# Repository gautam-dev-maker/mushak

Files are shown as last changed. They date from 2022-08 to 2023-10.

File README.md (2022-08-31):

<p align="center">
  
</p>

# About The Project

Mushak is a micromouse maze solving bot. The aim of this project is to make India's first and smallest half-size micromouse bot. "Mushak" in hindi means "Mouse".

This micromouse consist of a very small coreless motors (6 mm width and 10 mm length) and PCB as it's base . Since coreless motors doesn't provide enough torque for the movements of bot we used gear box to increase the torque.

Mushak is of size 45.7mm x 40.0 mm, which is smaller than similar micromouse using STM32F405RG. We boast of least area consuming micromouse made using STM32 LQFP64 package chips.

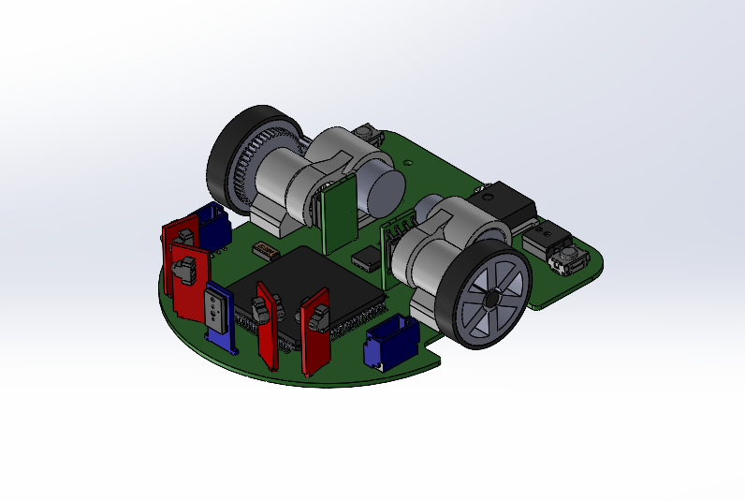
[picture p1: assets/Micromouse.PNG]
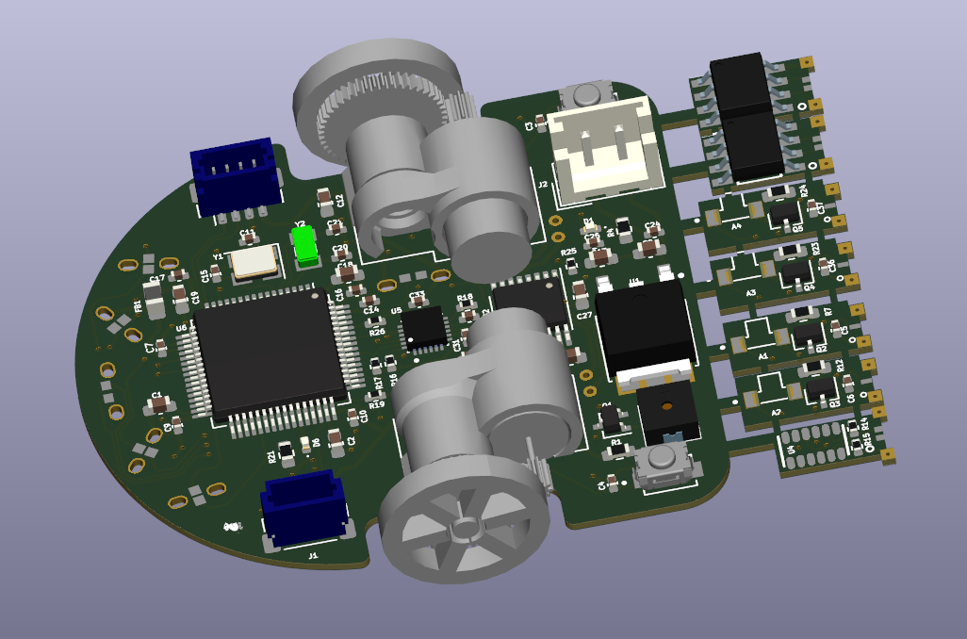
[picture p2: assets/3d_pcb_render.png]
|             |  |
:-------------------------:|:-------------------------:

# Table of Content
- [About The Project](#about-the-project)
- [Table of Content](#table-of-content)
- [File Structure](#file-structure)
- [PCB Design](#pcb-design)
    - [Major components used in the PCB include -](#major-components-used-in-the-pcb-include--)
  - [IR sensors](#ir-sensors)
    - [Placement of IR Sensors](#placement-of-ir-sensors)
  - [Power Distribution](#power-distribution)
  - [STM32F405RG (Microcontroller)](#stm32f405rg-microcontroller)
  - [DRV8833 (Motor Driver)](#drv8833-motor-driver)
  - [VL6180X (ToF Sensor)](#vl6180x-tof-sensor)
  - [HC-08 (BLE Module)](#hc-08-ble-module)
  - [AS5600 (Magnetic Encoder)](#as5600-magnetic-encoder)
  - [MPU6500 (IMU)](#mpu6500-imu)
  - [Routing](#routing)
  - [Solutions to some of the major problems faced while designing PCB](#solutions-to-some-of-the-major-problems-faced-while-designing-pcb)
- [CAD Design](#cad-design)
  - [Part Descriptions](#part-descriptions)
  - [Issues Faced in Mechanical Designing](#issues-faced-in-mechanical-designing)
    - [Designing Mount](#designing-mount)
    - [Finalising and Meshing the gears](#finalising-and-meshing-the-gears)
- [Firmware](#firmware)
  - [File Structure](#file-structure-1)
  - [Pinout of STM32F405RG](#pinout-of-stm32f405rg)
    - [Communication Buses](#communication-buses)
    - [ADC](#adc)
    - [PWM](#pwm)
    - [GPIO](#gpio)
  - [How To Use The Firmware](#how-to-use-the-firmware)
    - [Install gcc-arm-none-eabi compiler tool suite](#install-gcc-arm-none-eabi-compiler-tool-suite)
    - [Install ST-Link Toolchain](#install-st-link-toolchain)
    - [Build the source code](#build-the-source-code)
    - [Flash on the STM32 device](#flash-on-the-stm32-device)
- [Resources](#resources)
- [Acknowledgements](#acknowledgements)
- [License](#license)

# File Structure

    .
    ├── Assets             # Documentation files screenshots, gifs, videos of results
    ├── firmware           # contains required code for controlling the bot
    ├── pcb_design         # PCB files made in  kicad 6
    ├── cad_design         # CAD files of mushak (micromouse)
    ├── LICENSE            # License for this project
    └── README.md          # Contains documentation and information about this project

Further file structure of each folder is given in below sections.

# PCB Design

The Mushak PCB design is made on the latest version of KiCAD 6.

Mushak is designed over STM32F405RG microcontroller accomodated with various sensors and drivers for the micromouse.

We designed the smallest micromouse that is based on STM32F405RG microcontroller

<p align="center">
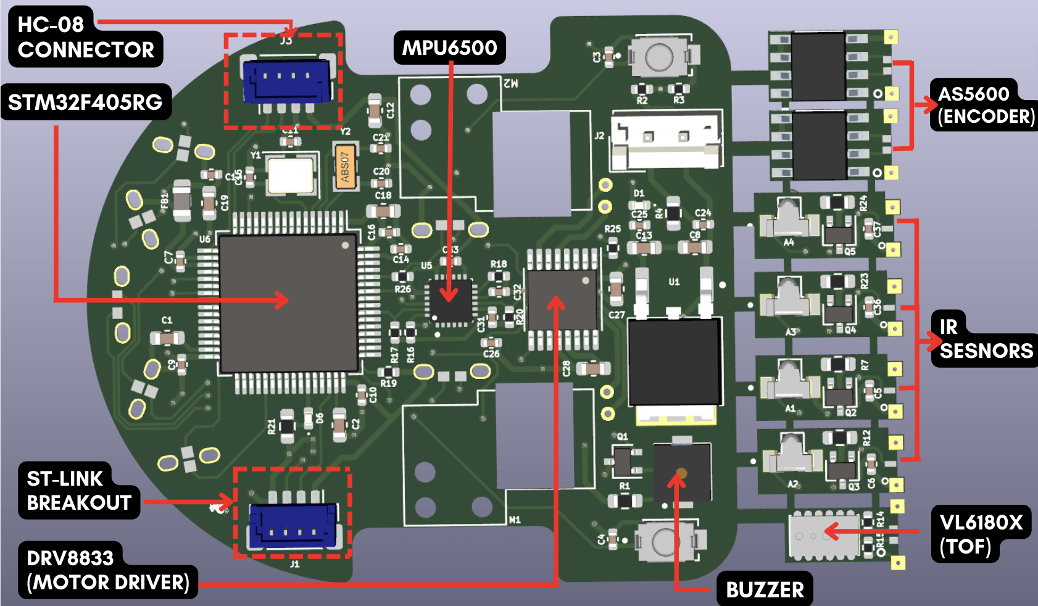
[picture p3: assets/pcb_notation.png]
  
</p>

### Major components used in the PCB include -

| Components | Description |
| --- | --- |
| STM32F405RG | Microcontroller |
| VL6180x | ToF sensor4 |
| DRV8833 | Motor Driver |
| MPU6500 | IMU |
| SFH-4045N | Infrared Emitter |
| SFH-3015-FA | Phototransistor (Reciever) |

---

## IR sensors

* The IR sensors include majorly two components, IR emitter which emits the Infrared light of a particular wavelength which is not visible with the human eye. 

* This light gets reflected back from the obstacle present in form of the robot to the photo transistor, when the Infrared light of this perticular wavelength enters the phototransistor device it allows the current to flow from the collector to the emmiter of device. This current flow creates a voltage drop across the resistor connected with the photo transistor and this voltage drop is read by th ADC of the microcontroller which varies as the intensity of light reflected changes. By this way we can determine how far is the obstacle from the robot.

* For controlling the intensity of the transmitted light we used N-Channel Mosfet whose gate is controlled by PWM signal given by the microcontroller.
By varying the PWM duty cycle we can control the intensity of the transmitted light from IR emmiter by which we can control the distance sensitivity.

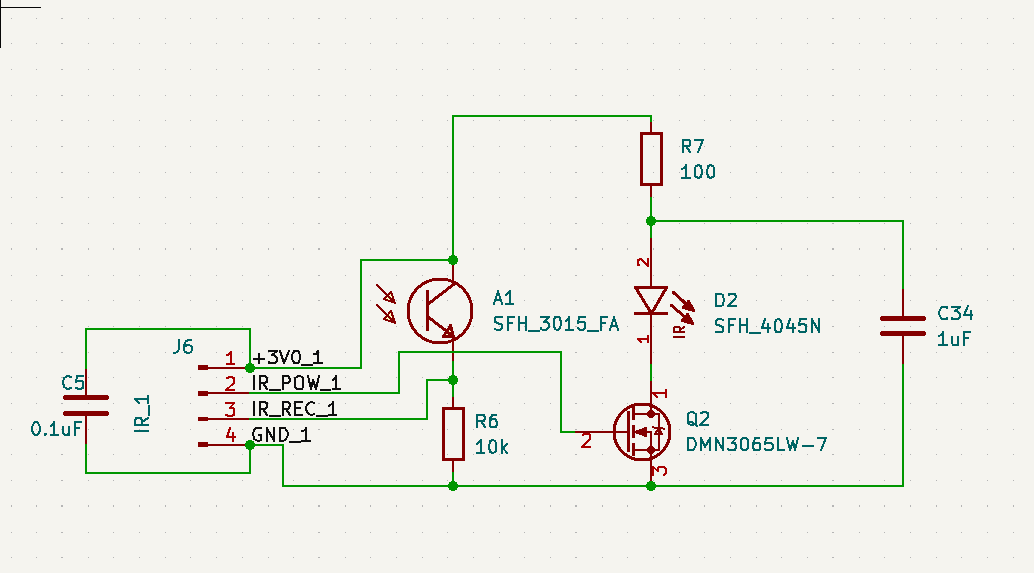
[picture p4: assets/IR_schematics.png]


* Four Sensor pairs are being used in Mushak (Micromouse)

### Placement of IR Sensors

Placing IR sensors pose a challenge, and required rigorous testing and brain storming. 

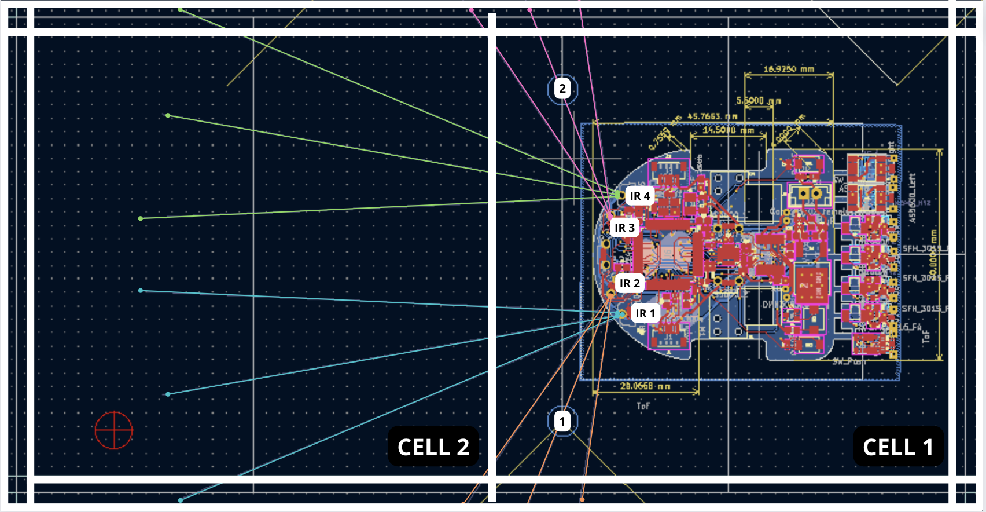
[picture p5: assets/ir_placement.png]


As can be seen in the image above we have visualised 2 cell based maze and bot is placed in first cell.

* `IR1` (blue rays) is pointing to the left mid point of next cell.
* `IR2` (orange rays) is pointing to the left end of current cell.
* `IR3` (pink rays) is pointing to the right end of current cell.
* `IR4` (green rays) is pointing to the right end of current cell.

To move the bot in straight line along the diagonal maze pattern , we have considered `point 1` and `point 2`. These two points are the edges of diagonal ends of above pattern . So if bot had to move diagonally we can check for readings at these two points and control the bot accordingly.

---

## Power Distribution
* Power to the control circuits is provided by 3V linear Regulator(LDO) which can provide upto 1A current. Power to the motor is directly given to the motor driver through battery.
* Additional capacitors are added across outputs for filtering out the voltage. Voltage divider resistors are being used to monitor the battery voltage. Power indication LED has been provided in the PCB. The input voltage for the PCB is 3.7 voltage through a general LiPo battery.

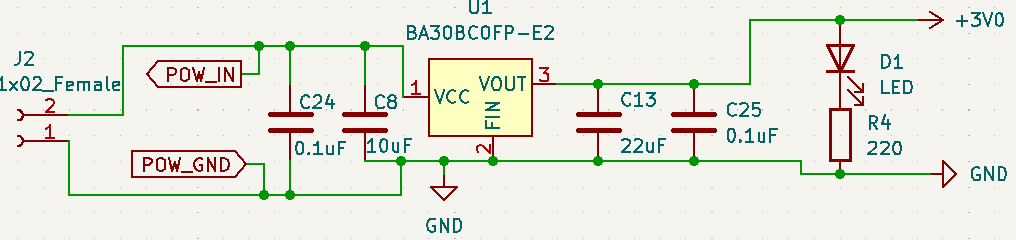
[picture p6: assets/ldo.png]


--- 

## STM32F405RG (Microcontroller)

The below image shows the pinout of STM32F405RG that we will be using for this project :

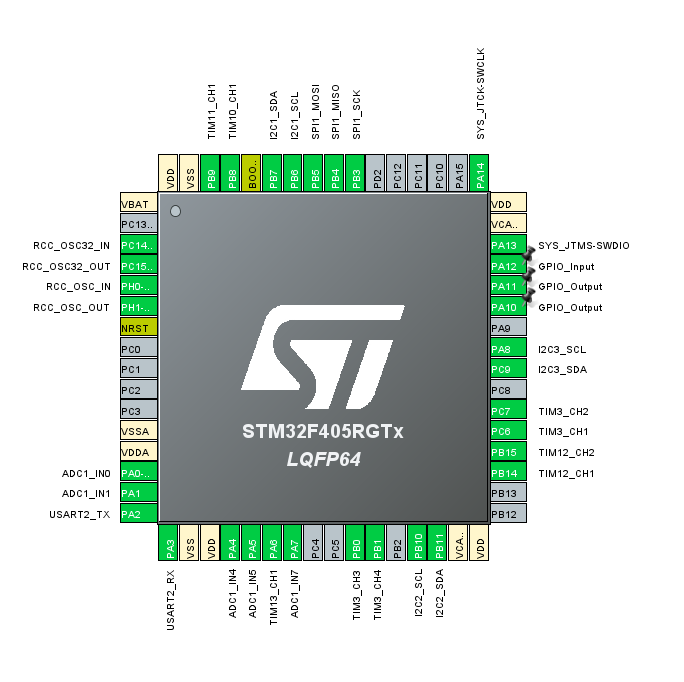
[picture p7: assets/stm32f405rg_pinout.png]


Decoupling capacitors of 0.1uF are connected near the vdd pins of STM32. Additional external low and high frequency oscillators are added for precise timing.

- HSE(High Speed External) clock - 25 Mhz
- LSE(Low Speed External) clock - 32.769 Khz

Filter circuit is being used for filtering out the analog reference voltage. Additional Debug switches are being added for debugging purposes

---
## DRV8833 (Motor Driver)

* We have used H-bridge motor driver which can control two motors at the same time via PWM (pulse width modulation) from the STM32F405RG (microcontroller).

* The motor driver can supply 1.5 Amps of current per motor which is enough to power up the coreless motors. 

* This motor driver keeps the controls terminals from the microcontrolller isolated from noise and high volatages of the motor power supply.

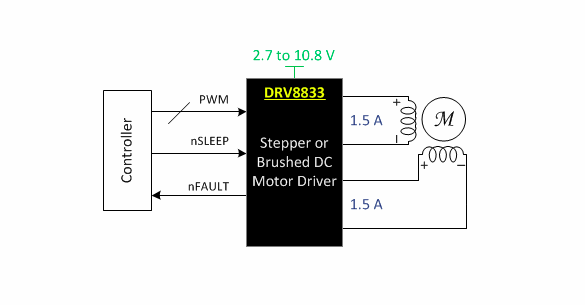
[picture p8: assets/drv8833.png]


---

## VL6180X (ToF Sensor)

* We added a Time of Flight sensor in front of the robot to measure the distance of the obstacle in front from the robot.

* This sensor measures the time taken by the light signal to get reflected from the obstacle and then measures the distace of the obstacle from the robot.

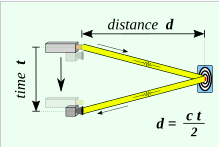
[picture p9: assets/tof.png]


* The sensor uses I2C protocol for communication with the microcontroller and send the distance values. It also has an additional feature of sensing the ambeint light which we can use to avoid the problems faced with IR sensors due to varing ambient light conditions.
* Due to cost issues it is not feasible to replace IR sensors with VL6180x, else it could have been a replacement.

---

## HC-08 (BLE Module)

* We used a BLE(Bluetooth Low Energy) module to communicate to the robot. It is one of the most important modules that is being used in mushak, this bluetooth module will enable us to communicate with the robot and precisely tune it to solve the mazes, additionally it makes debugging easier for us making Mushak user friendly.

* The module consumes very less power(since it works on BLE) and works on UART communication to talk with the microcontroller.

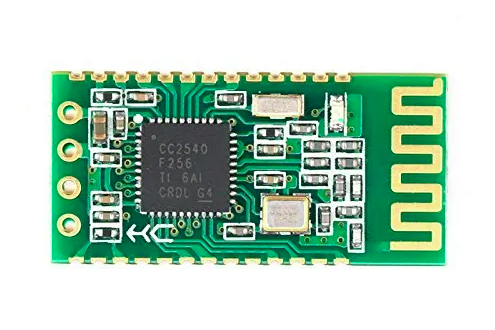
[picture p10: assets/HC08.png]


* For attaching this module we have provided the JST connectors to connect this module externally when required.

---

## AS5600 (Magnetic Encoder)

* To measure the RPM and the distance that the robot has covered we needed a type of encoder feedback. For this we used AS5600 magnetic encoders to measure the amount of rotation of the robot wheel.

* The magnetic encoders are mounted in an innovative way due to which no external mounts were required for their placement. Since magnets need to be right infront of the IC of AS5600 to get proper reading, we have taken extra care with mount size and shaft placement.

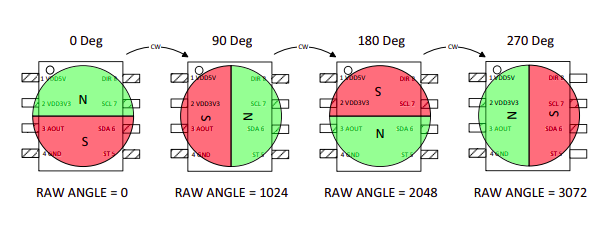
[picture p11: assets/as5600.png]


* The sensor works on I2C communication protocol to provide the reading to the microcontroller.

---

## MPU6500 (IMU)

* This sensor gives the feedback of orientaion of the robot. This MEMS based chip has in-built Acclereometer and Gyroscope by which it can determine its orietation with respect to space.

* This sensor works on SPI as well as I2C communication protocol but in our case to get the fastest data transfer, we used use SPI communcation.

---

## Routing

* Front Copper Layer:

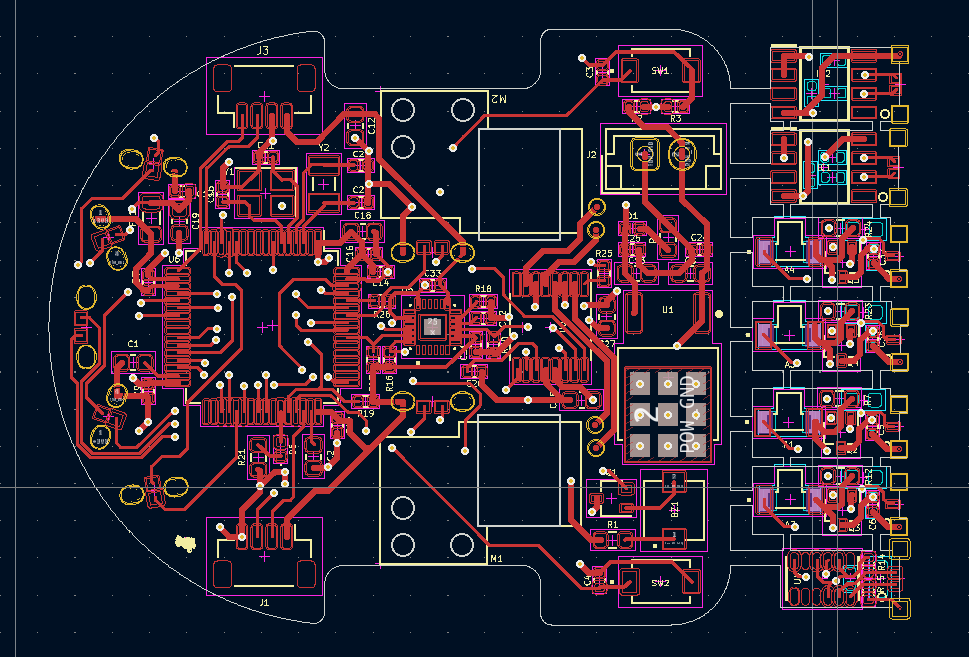
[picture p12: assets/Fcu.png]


* Back Copper Layer:

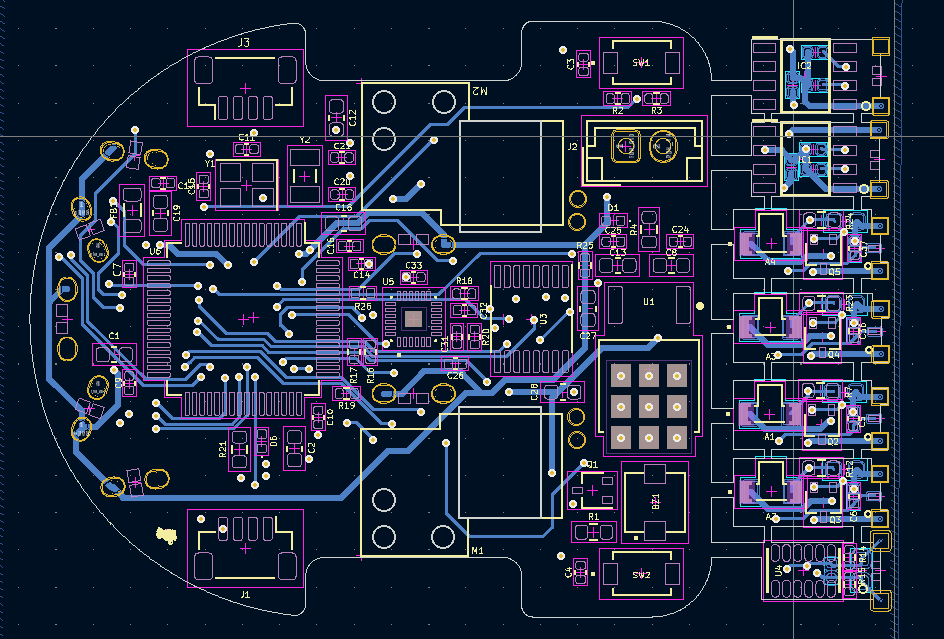
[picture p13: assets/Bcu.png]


* Final Routing:

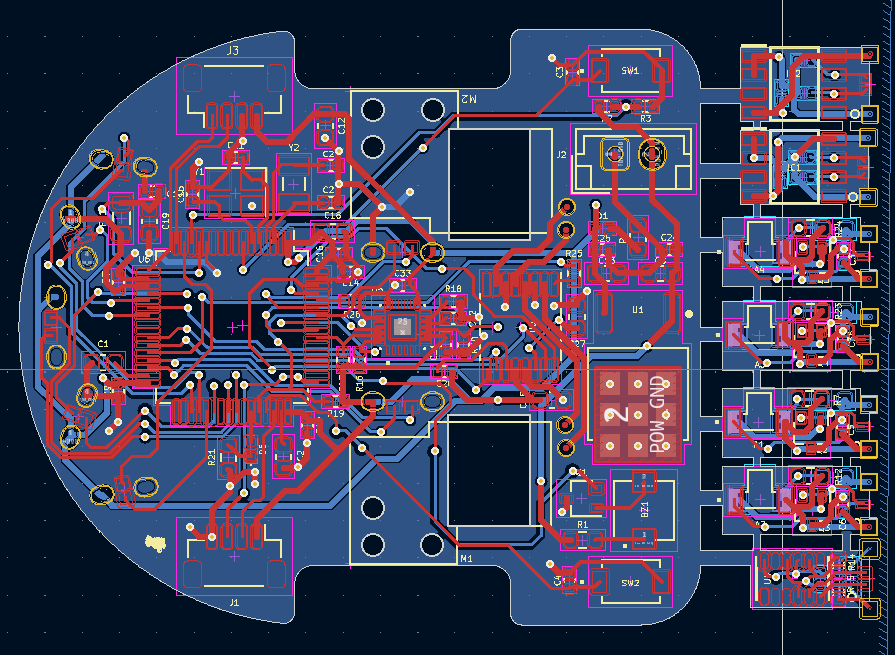
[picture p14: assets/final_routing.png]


For routing of the control circuitry we used traces of 0.2mm width and for power connections we used 0.4mm width tracks to ensure fairly high current flow.

## Solutions to some of the major problems faced while designing PCB

1) Minimalising passive components is a really hard task. So to solve this I properly reffered the application notes and datasheet of stm32f405RG. Moreover the design is well tested on simulation platform.

2) Efficient placement of components to reduce the size of the PCB. Innovative design to fix sensors and encoders in such a small space.

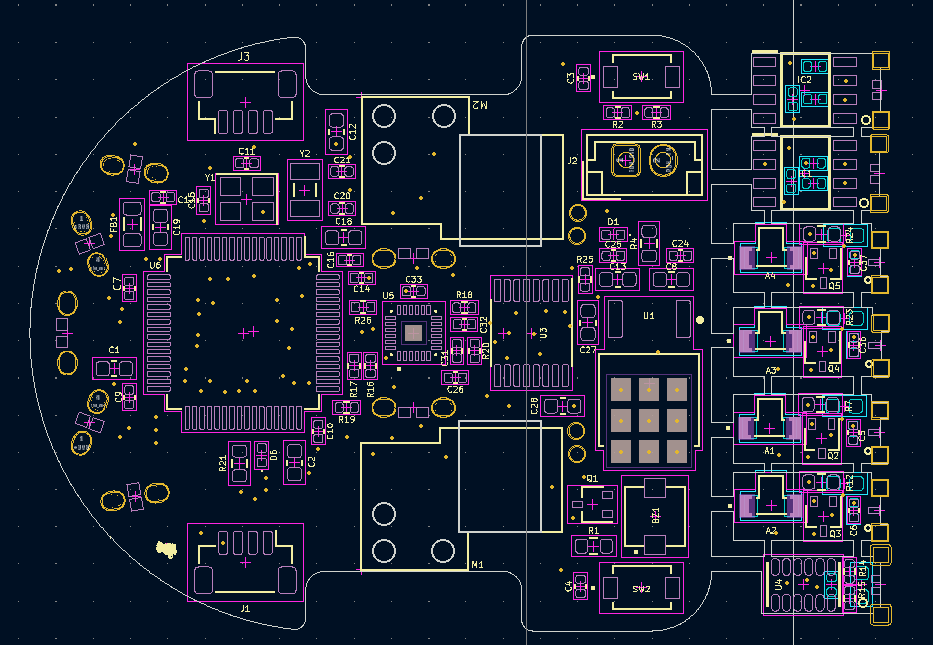
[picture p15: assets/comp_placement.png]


3) Since IRs are sensitive to ambient light we required a mechanism to adjust the brighness of IR Emitter. So to do that we used a mosfet based circuit, so brightness can be controlled using PWM.

4) It was a big challenge to place 90+ SMD and THT components on a small size PCB of just 45.7x40mm size.

# CAD Design

CAD design consist of 3D modeling of Bot design.Before design can be made on PCB, we need to check if various other aspects of systems and mechanical design satisfy our requiements. So CAD design form a very important part of our project.

## Part Descriptions
* The bot contains a total of 6 main **mechanical** components which are as listed in the following table :

| Parts | Description |
| --- | --- |
| <p align="center">
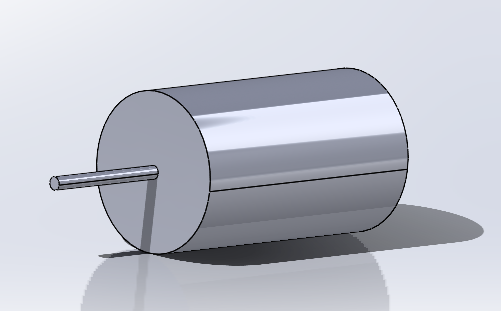
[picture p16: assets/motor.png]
   | Motors - This motor has </br> dimensions: Length x Dia. 12 x 6 mm and a shaft lenght of 6mm.|
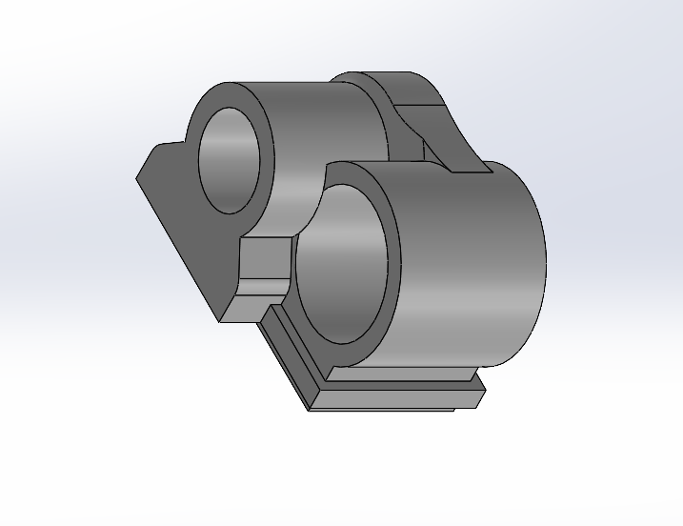
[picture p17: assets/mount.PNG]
   | Motor_mount - This is the mount for the motors, which holds </br> the motor, shaft, gears, bearing and magnet.Because of less center-to-center distance between gears, after many iterations this mount was designed.|
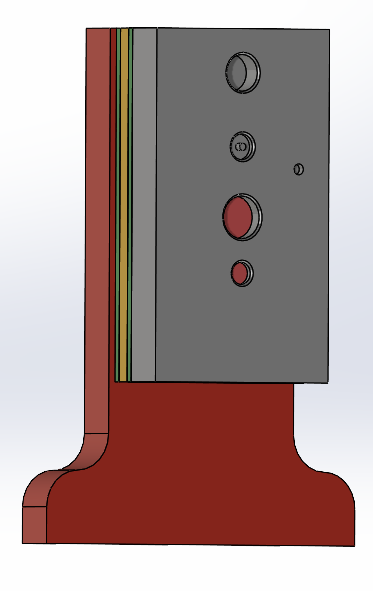
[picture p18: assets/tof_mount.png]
   | TOF_mount - This is the mount for TOF sensor, which is placed </br> in front. We have used VL6180x TOF sensor.|  
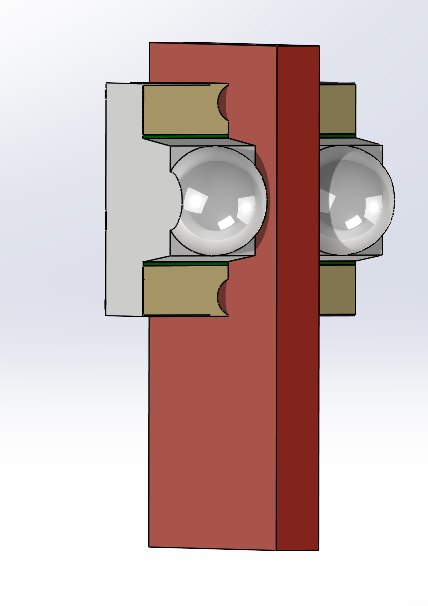
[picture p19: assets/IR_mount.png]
    | IR_mounts - These are the mounts for IR sensors placed </br> at specific angles. SFH-3015-FA and SFH-4045N sensors are phototransistors and IR emitters respectively.|   
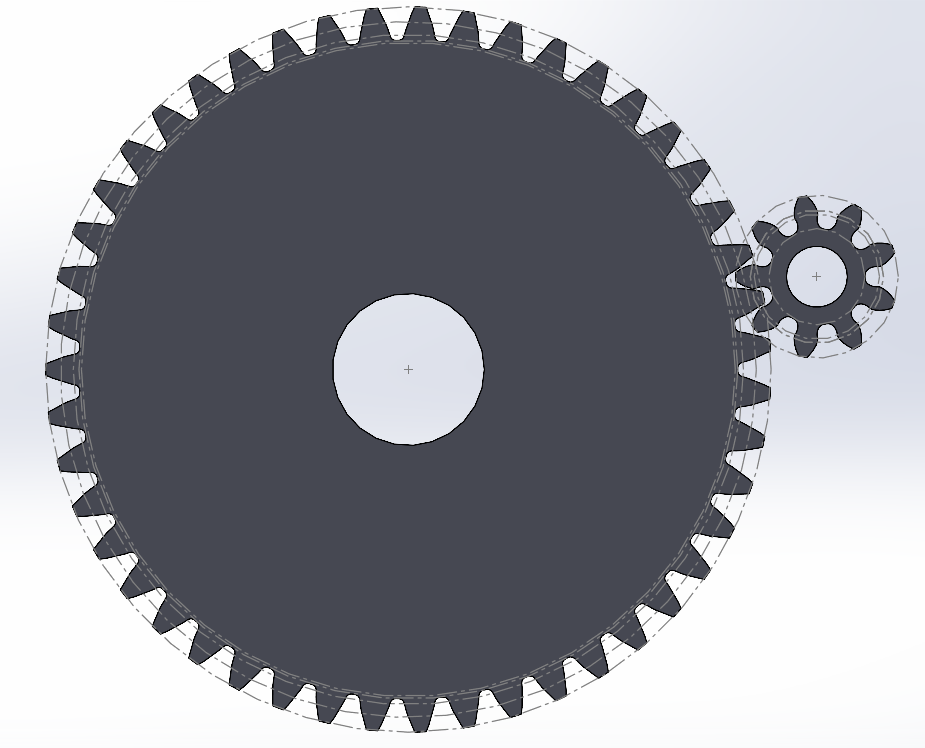
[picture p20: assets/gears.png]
    | Gears - The metal gears were extracted from mg90s servos having dimensions: </br> Driving gear:</br> &emsp; &emsp; &emsp;&emsp; &emsp;Teeth 9 </br> &emsp; &emsp; &emsp;&emsp; &emsp;Pressure Angle - 20º</br> &emsp; &emsp; &emsp;&emsp; &emsp;ID - 0.5, OD - 2.14 mm</br> &emsp; &emsp; &emsp;&emsp; &emsp;Width 2.46 mm</br> Driven gear: </br> &emsp; &emsp; &emsp;&emsp; &emsp;Teeth 47 </br> &emsp; &emsp; &emsp;&emsp; &emsp;Pressure Angle 20º</br> &emsp; &emsp; &emsp;&emsp; &emsp;ID - 1.5mm, OD - 9.55 mm</br> &emsp; &emsp; &emsp;&emsp; &emsp; Width 1.2 mm.</br> Center to center distance is 5.80mm and modulus 0.195</br>| 
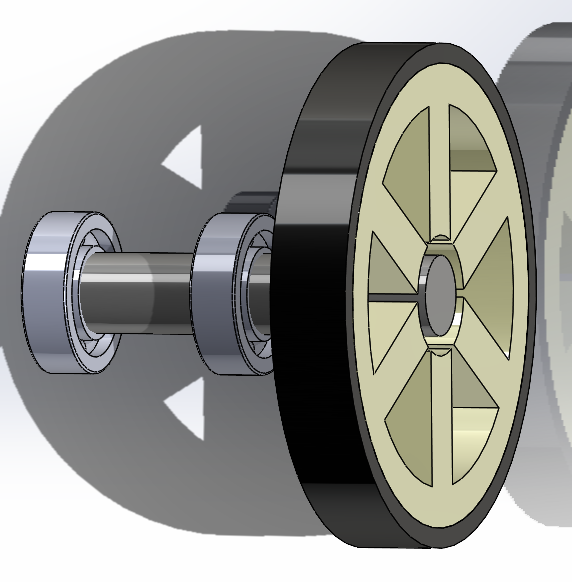
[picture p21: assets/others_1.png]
    | Bearings, shaft and Wheels - These are the passive components used.</br> Bearings x4 of dimensions: ID x OD 1.5 x 4 mm.</br> Shaft x2 of dimensions: Length x Dia. 15 x 1.5 mm.</br> Wheels with dimensions: ID x OD 1.5 x 12.5 mm.</br> A combination of 2 bearings is used to house the shaft for better stability and lesser Vibrations.|
</p>

**NOTE** : 
* ID is abbreviation for Internal Diameter.
* OD is abbreviation for Outer Diameter.

## Issues Faced in Mechanical Designing 
### Designing Mount 
  
* **Issue** : The main issues faced in designing the Mount were As the Gears acquired were of a smaller diameter, there was an issue of interference between the bearing and the motor. As they were too close, it was impossible to 3D print a mount with the thickness less than 1mm.
* **Solution** : The solution opted for this was to actually disalign the motor and the shaft to give room the bearing housing to be 3D printed. This enabled us to print a more stable base due to the stronger Shaft housing.
Below images demonstrate how it was done.

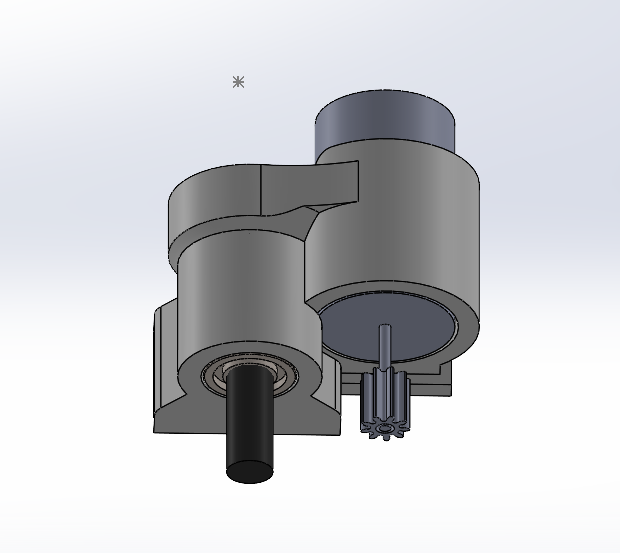
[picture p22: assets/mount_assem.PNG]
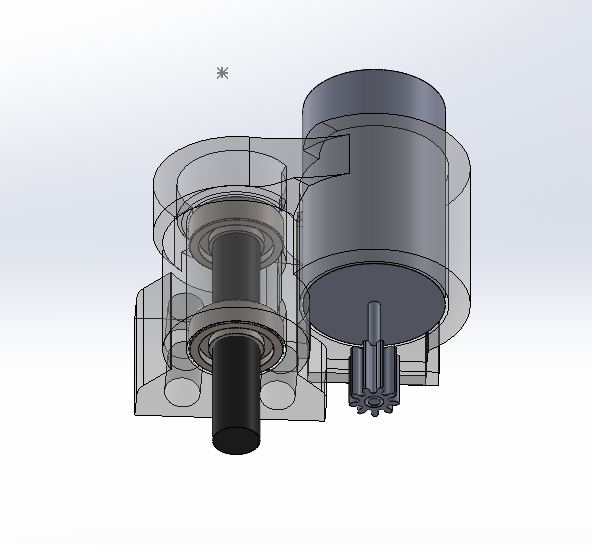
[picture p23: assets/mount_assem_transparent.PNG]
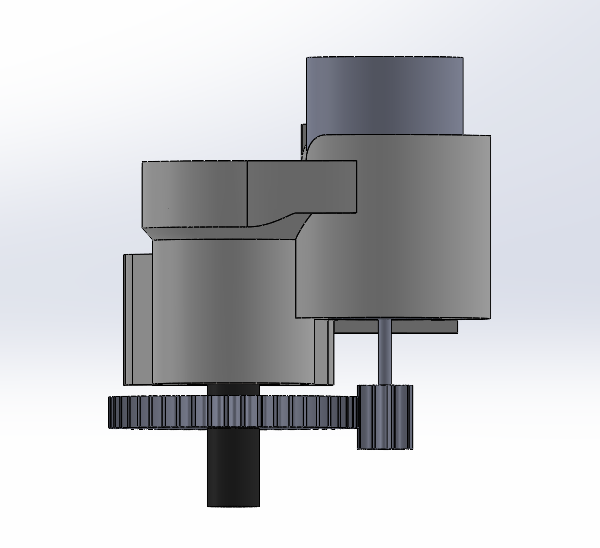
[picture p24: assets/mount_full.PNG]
|             |  |  |  |
:-------------------------:|:-------------------------:|:-------------------------:|:-------------------------:
  
### Finalising and Meshing the gears
  
* **Issue** : As there are a varieties of gears available. It was hard for us to choose the right combination and Built the Model and mounts around it.
* **Solution** : We started with finalising the sizes and the gear ratios needed according to the available spaces. We then did the market research to find the gears closest to our needs and incorporated those models into the Design.

<p align="center">

# Firmware

The firmware for this project is written using STM32-HAL. STM32 HAL consist of bare-metal register address and light weight peripheral libraries giving programmer the full control. For running multiple tasks we are using [FreeRTOS](https://www.freertos.org). We will be storing the maze in flash memory, since page size is 2 bytes, we need to access 2 bytes at a a time. 

The firmware is required to interact with the following external sensors/peripherals: 

- [SFH-4045N](https://dammedia.osram.info/media/resource/hires/osram-dam-2496064/SFH%204045N.pdf) : Infrared Emitter for detecting walls.
- [SFH-3015-FA](https://dammedia.osram.info/media/resource/hires/osram-dam-2495986/SFH%203015%20FA.pdf) : Infrared Receiver to receive the emitted 
- [AS5600-ASOT](https://ams.com/documents/20143/36005/AS5600_DS000365_5-00.pdf) : Encoders to calculate the movements of wheel.
- [DRV8833](https://www.ti.com/lit/ds/slvsar1e/slvsar1e.pdf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) : Dual H-bridge Motor driver required to control motor.
- [MPU6500](https://invensense.tdk.com/wp-content/uploads/2020/06/PS-MPU-6500A-01-v1.3.pdf) : Gyroscope and Accelerometer sensor.
- [SMT-0440-S-R](https://www.puiaudio.com/media/SpecSheet/SMT-0440-S-R.pdf) : buzzer to generate the victory sound.
- [VL6180x](https://www.st.com/resource/en/datasheet/vl6180x.pdf) : Time of flight sensor to measure the distance between wall and bot.
- [HC-08](http://www.hc01.com/downloads/HC-08A%20version%20english%20datasheet.pdf) : Bluetooth module primarily used for logging. It uses 9600 baud rate for communication.

## File Structure

    .
    ├── Firmware                                # contains required code for controlling the bot
    │    ├── Core                               # Contains developer code for sensors and other peripherals
    │    │   ├── As5600                         # Driver Api for AS5600
    │    │   │   ├── as5600.c                   # Source code for AS5600
    │    │   │   └── as5600.h                   # Header file for AS5600
    │    │   ├── Ble_logger                     # Bluetooth logger API using UART
    │    │   │   ├── ble_logger.c               # Bluetooth logger source code
    │    │   │   └── ble_logger.h               # Bluetooth logger header file
    │    │   ├── Drv8833                        # Code for Motor Control
    │    │   │   ├── drv8833.c                  # Source code for DRV8833
    │    │   │   └── drv8833.h                  # Header files for DRV8833
    │    │   ├── Inc                  
    │    │   │   ├── FreeRTOSConfig.h           # FreeRTOS configuration file
    │    │   │   ├── main.h                     # Main header file
    │    │   │   ├── stm32f4xx_hal_conf.h       # STM32 HAL configuration file
    │    │   │   └── stm32f4xx_it.h             # contains header of interrupt handlers
    │    │   ├── Mpu6500
    │    │   │   ├── mpu6500.c                  # Source code for MPU6500 Driver
    │    │   │   └── mpu6500.h                  # Header file for MPU6500 Driver
    │    │   ├── Peripheral                     
    │    │   │   └── I2c                        # I2C API's handler
    │    │   ├── Src
    │    │   │   ├── freertos.c                 # FreeRTOS source code
    │    │   │   ├── main.c                     # Main source code
    │    │   │   ├── stm32f4xx_hal_msp.c        # MSP initialisation and deinitialiation source code
    │    │   │   ├── stm32f4xx_it.c             # source code for interrupt handlers
    │    │   │   └── system_stm32f4xx.c         # CSMSIS peripheral device layer source code
    │    │   └── Vl6180x
    │    │       ├── vl6180x.c                  # VL6180x Driver source code
    │    │       └── vl6180x.h                  # VL6180x header file
    │    ├── Drivers                            # STM32 Driver Code involving bare metal registers
    │    ├── Middlewares                        # FreeRTOS APIs for scheduling algorithm
    │    ├── node_modules                       # HTML modules for viewing STM32 HAL API documentation
    │    ├── Makefile                           # Automake compilation instructions
    │    ├── STM32F411CEUx_FLASH.ld             # Linker script for compilation   
    └────└── node_modules                       # HTML modules for viewing STM32 HAL API

## Pinout of STM32F405RG

The below image shows the pinout of STM32F405RG that we will be using for this project :



### Communication Buses

- **I2C (Inter-Integrated Circuit)** : We use two encoders(*AS5600*),so we needed to use two different I2C bus. *Vl6180x* (ToF) sensor also uses I2C bus communication, so overall 3 I2C bus communication is used.
- **SPI (serial peripheral interface)** : *MPU6500* supports both I2C as well as SPI, but since SPI offers faster communication , we decided to go with it.
- **UART (Universal Asynchronous Receiver/Transmitter)**: *HC-08* bluetooth module , which will be used for logging functions on UART transmission protocol.

### ADC

- SFH-3015-FA (IR receiver) gives analog signals, so it requires ADC module to read the readings. So we require 4 ADC channels for reading IR sensors
- To measure voltage level of battery one ADC channel will be required

So overall 5 ADC channels are required.

### PWM

- DRV8833 (Dual H-bridge Motor Driver) requires 4 PWM channel.
- To control the brightness of 4 SFH-4045N (IR emitter) we need 4 more PWM channels
- To generate noise in the buzzer we will need 1 more PWM channel.

So in overall we will require 9 PWM channels.

### GPIO

- 2 GPIOs are required for 2 LEDs
- 1 GPIOs are required for 1 Button

so In overall 3 GPIO pins are used for getting input and output.

## How To Use The Firmware

### Install gcc-arm-none-eabi compiler tool suite

* ### For Linux 

```
sudo apt-get update
sudo apt-get install -y gcc-arm-none-eabi
```

* ### For MacOS
```
brew tap ArmMbed/homebrew-formulae
brew install arm-none-eabi-gcc
```
### Install ST-Link Toolchain

* ST-Link toolchain is required for flashing on STM32 chip.

* ### For Linux
```
sudo apt-get update
sudo apt-get -y install stlink-tools
```

* ### For MacOS

```
brew install stlink
```

### Build the source code

* ### Clone the reponsitory and change the directory to firmware

```
git clone https://github.com/gautam-dev-maker/mushak.git
cd mushak/firmware
```

* ### Build using make tool
```
make -j4  # based on no. of logical cores available in your system
```

### Flash on the STM32 device

```
make flash  # Currently only st-link support is added
```

# Resources
* [Project Futura](http://micromouseusa.com/?page_id=1342) is a tutorial for micromouse designing
* [Micromouse Tyre](http://micromouseusa.com/?page_id=1342) a blog related how to select the tyres for micromouse
* [Phase-lead controller](https://micromouseonline.com/2011/05/16/designing-a-phase-lead-controller/) an alternative to PID control systems for micromouse.
* [Slip Compensation](https://robotics.stackexchange.com/questions/1658/implementing-slip-compensation-into-a-half-size-micromouse) discussion on how to compensate slip in micromouse which becomes a serious issue
* [Kerise v5](https://github.com/kerikun11/micromouse-kerise-v5) Smallest micromouse ever made, contains good documentation of design,pcb and code.
* [SolidWorks Tutorial](https://www.youtube.com/watch?v=Ulttc_2p4DY&list=PLrOFa8sDv6jcp8E3ayUFZ4iNI8uuPjXHe) to sharpen your skills in SolidWorks.

# Acknowledgements
* [SRA VJTI](http://sravjti.in) for providing us with required resources and support.
* [Ryotaro Onuki](https://github.com/kerikun11) for helping with all the designs and technical aspect of micromouse. His willingness to share his experience and answering our question has led to the start of the project.

# License
The [License](https://github.com/gautam-dev-maker/mushak/blob/master/LICENSE) Used for this Project.

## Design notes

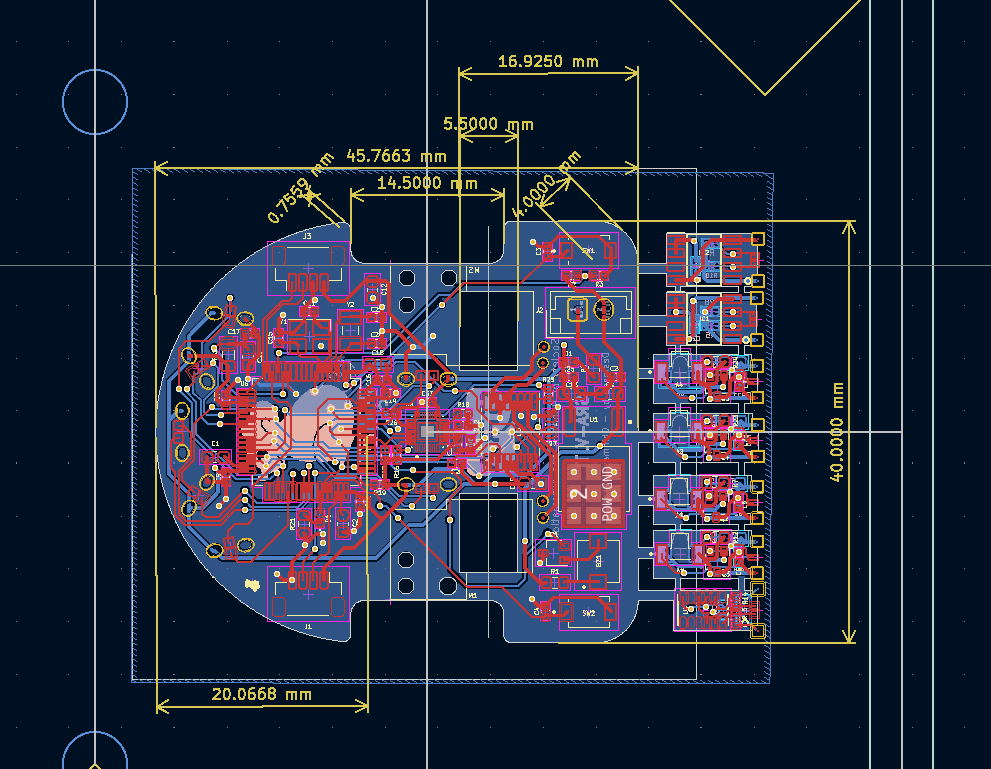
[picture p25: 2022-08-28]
assets/pcb_routing.png

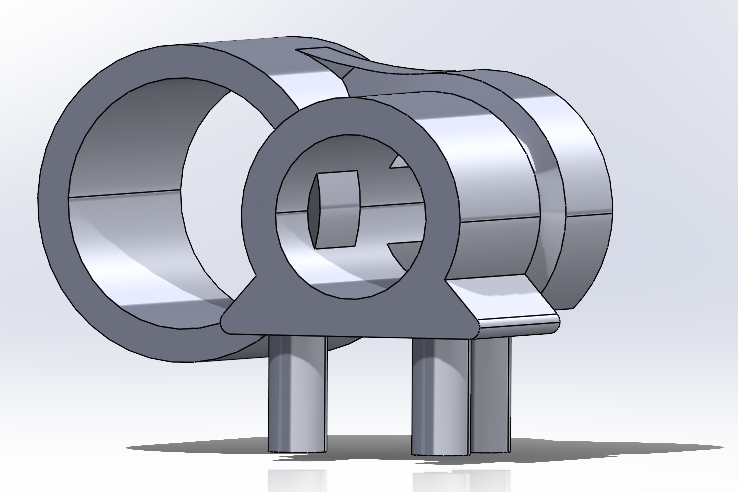
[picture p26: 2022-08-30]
assets/motor_mount.png

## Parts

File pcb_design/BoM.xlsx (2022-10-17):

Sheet: main_final_BOM
 |  |  |  | MUSHAK BILL OF MATERIALS
purchase later |  | to purchase
already purchased |  | remove from module
 |  |  |  |  |  |  | f
Ref | Quantity | Value | Manufacture Part Number | Footprint | Description | Vendor (Digikey) | Vendor (Mouser) | Indian Vendor (best price) | Best Buy (₹ / piece) inc. GST | Cost per build (₹) | Purchase Qty | Overall cost (₹) 40% off on Evelta for min. 10 piece | Comments | Cost per build ($) | LCSC | Cost ($)
A1, A2, A3, A4, | 4 | SFH_3015_FA | SFH 3015 FA | SFH_3015_FA:XDCR_SFH_3015_FA | IR_Reciever | SFH_3015_FA (₹49.86/10piece) (https://www.digikey.in/en/products/detail/ams-osram-usa-inc/SFH-3015-FA/2415039) | SFH_3015_FA (₹40.86/10piece) (https://www.mouser.in/ProductDetail/ams-OSRAM/SFH-3015-FA?qs=JdgXXoipWqUDlNTnoH77ZA%3D%3D) | Not available in India | 59.93 | 239.72 | 10 | 498.58 | Not available on Indian sites ( Already ordered from semikart) |  | out of stock
BZ1, | 1 | Buzzer | SMT-0440-T-R | SMT-0440-T-R:XDCR_SMT-0440-T-R | Buzzer, polarized | digikey (https://www.digikey.in/en/products/detail/pui-audio-inc/SMT-0440-T-R/5113608) | mouser (https://www.mouser.in/ProductDetail/PUI-Audio/SMT-0440-T-R?qs=7PCaVhlmG1oC7sD2lJM0%2Fg%3D%3D) | semikart(digikey) (https://www.semikart.com/search/SMT-0440-T-R) | 247.69 | 247.69 | 1 | 247.69 | SMD version not available in India |  | discontinued
C1, C2, C27, | 3 | 2.2uF | CL10A225KP8NNNC | Capacitor_SMD:C_0603_1608Metric | Unpolarized capacitor | 2.2uF_0402 (₹18.46/10piece) (https://www.digikey.in/en/products/detail/tdk-corporation/C1005JB1A225K050BC/3948140) | 2.2uF_0402 (₹11.69/10 piece) (https://www.mouser.in/ProductDetail/Kyocera-AVX/CM05X7S225M06AH065?qs=A6eO%252BMLsxmS301H7ZRkNqA%3D%3D) | evelta (https://www.evelta.com/2-2uf-10v-10-x5r-0603-ceramic-capacitor/) | 8.26 | 24.78 | 10 | 49.56 | 0603 package available | 0.27 | C417153 (https://www.lcsc.com/product-detail/Multilayer-Ceramic-Capacitors-MLCC-span-style-background-color-ff0-SMD-span-SMT_Murata-Electronics-GRM155R61C225ME11D_C417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) | 0.09
C14,C3, C4, C5, C6, C7, C9, C10, C16, C30, C32, C33, C36, C37, C24, C25, C40, C41 | 18 | 0.1uF | CC0402KRX7R9BB104 | Capacitor_SMD:C_0402_1005Metric | Unpolarized capacitor | 0.1uF_0402 (₹2.32/10piece) (https://www.digikey.in/en/products/detail/walsin-technology-corporation/0402B104K160CT/6707534) | 0.1uF_0402 (₹3.34/10 piece) (https://www.mouser.in/ProductDetail/Kyocera-AVX/04023C104KAT4A?qs=XLNwXgtzMM%2FjcUD%2FzDf3Ww%3D%3D) | evelta (https://www.evelta.com/100nf-50v-10-x7r-0402-ceramic-capacitor/) | 2.12 | 38.16 | 35 | 44.6 | pack of 35 | 0 | discontinued
C13, | 1 | 22uF | CC603MRX5R6BB226 | Capacitor_SMD:C_0603_1608Metric | Unpolarized capacitor |  |  | ktron (https://www.ktron.in/product/22uf-10v-ceramic-capacitor-mlcc-smd-0603/?hsa_acc=6332829093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) | 1.42 | 1.42 | 15 | 21.24 |  | 0 | 0402 not found
C11, C15, | 2 | 22pF | 0402N220J500CT | Capacitor_SMD:C_0402_1005Metric | Unpolarized capacitor | digikey (https://www.digikey.in/en/products/detail/kyocera-avx/0402YA200JAT2A/1597704) | 20 pF (12.41/10 piece) (https://www.mouser.in/ProductDetail/Kyocera-AVX/04025A200JAT2A?qs=HeiVa0IqVQ2m4eBQNX5O9Q%3D%3D) | evelta (https://www.evelta.com/22-pf-50v-0402-smd-multi-layer-ceramic-capacitor-0402n220j500ct-walsin/) | 3.96 | 7.92 | 10 | 23.76 | got 22pF instead of 20pF | 0 | discontinued
C12, C19, C34, C35, C38, C39, | 6 | 1uF | CC0603KRX5R9BB105 | Capacitor_SMD:C_0603_1608Metric | Unpolarized capacitor | digikey (https://www.digikey.in/en/products/detail/kyocera-avx/04023D105KAT2A/13557232) | mouser (https://www.mouser.in/ProductDetail/Taiyo-Yuden/GMK105CC6105KV-F?qs=pUKx8fyJudABY0rk3n4wKw%3D%3D) | ktron (https://www.ktron.in/product/1uf-50v-ceramic-capacitor-mlcc-smd-0603/) | 1 | 6 | 20 | 12 | got 0603 package | 0.1878 | C913450 (https://www.lcsc.com/product-detail/Multilayer-Ceramic-Capacitors-MLCC-span-style-background-color-ff0-SMD-span-SMT_Murata-Electronics-GRM155R70J105MA12D_C913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) | 0.0313
C17,C31,C26, | 3 | 0.01uF | CC0402KRX7R9BB103 | Capacitor_SMD:C_0402_1005Metric | Unpolarized capacitor | digikey (https://www.digikey.in/en/products/detail/taiyo-yuden/HMK105B7103MVHFE/11687499) | mouser | evelta (https://www.evelta.com/10-nf-50v-0402-smd-multilayer-ceramic-capacitors-cc0402krx7r9bb103-yageo/) | 0.59 | 1.77 | 10 | 3.54 |  | 0 | discontinued
C18, C28, C8, C23, C22 | 5 | 10uF | CL10A106MQ8NNNC | Capacitor_SMD:C_0603_1608Metric | Unpolarized capacitor | digikey (https://www.digikey.in/en/products/detail/samsung-electro-mechanics/CL05X106MR5NUNC/5961263) | mouser (https://www.mouser.in/ProductDetail/Kyocera-AVX/CM21X5R107M06AT?qs=Znm5pLBrcAI44q2aWOSJYQ%3D%3D) | evelta (https://www.evelta.com/10uf-6-3v-20-x5r-0603-capacitor/) | 3.54 | 17.7 | 10 | 21.24 | got 0603 package | 0.556 | C703695 (https://www.lcsc.com/product-detail/Multilayer-Ceramic-Capacitors-MLCC-span-style-background-color-ff0-SMD-span-SMT_Murata-Electronics-ZRB15XR60J106ME12D_C703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) | 0.1112
C20, C21, | 2 | 12pF | CC0402JRNPO9BN120 | Capacitor_SMD:C_0402_1005Metric | Unpolarized capacitor |  |  | evelta (https://www.evelta.com/12-pf-50v-0402-smd-multilayer-ceramic-capacitors-cc0402jrnpo9bn120-yageo/) | 2.5 | 5 | 10 | 15 | got 12 pF instead of 12.5pF | 0 | discontinued
C29, | 1 | 4.7uF | CL10A475KP8NNNC | Capacitor_SMD:C_0603_1608Metric | Unpolarized capacitor | digikey (https://www.semikart.com/product/osram-opto-semiconductors-/SFH-3015-FA/1858984) | mouser (https://www.mouser.in/ProductDetail/Kyocera-AVX/CM05X5R475M25AH?qs=MyNHzdoqoQJvFdZaEuclBg%3D%3D) | evelta (https://www.evelta.com/4-7uf-10v-10-x5r-0603-capacitor/) | 4.72 | 4.72 | 10 | 28.32 | got 0603 package | 0 | discontinued
D1, D6, | 2 | LED | RD-LED-0402 | LED_SMD:LED_0402_1005Metric | Light emitting diode | -- | -- | evelta (https://www.evelta.com/rd-led-0402-red-led-smd-0402-high-brightness-surface-mount-led/) | 3.1 | 6.2 | 10 | 48.97 | other colours are cheaper but I went for green | 0
D2, D3, D4, D5, | 4 | SFH_4045N | SFH 4045N | SFH_4045N:LED_SFH_4045N | IR_transmitter | SFH_4045N (₹51.14) (https://www.digikey.in/en/products/detail/ams-osram-usa-inc/SFH-4045N/4360733) | SFH_4045N (₹52.47) (https://www.mouser.in/ProductDetail/ams-OSRAM/SFH-4045N?qs=9EKcitwk7VRzbAsL4%252B52Qg%3D%3D) | Not available in India | 51.14 | 204.56 | 10 | 337.98 | Not available on Indian sites (digikey) ( Already ordered from semikart) | 0 | unavailable
FB1, | 1 | 120R | UPZ2012E121-4R0TF | Inductor_SMD:L_0805_2012Metric | Ferrite bead, small symbol |  |  | evelta (https://www.evelta.com/120ohm-4a-25-0805-ferrite-bead/) | 2.11 | 2.11 | 10 | 12.66 | I want to make sure if this component is correct | 0 | out of stock
U2, U7 | 2 | AS5048B-HTSP | AS5048B-HTSP | AS5048B-HTSP:SOP65P640X120-14N | Magnetic Encoder | digikey (https://www.digikey.in/en/products/detail/ams/AS5048B-HTSP/7383479?cur=INR&lang=en&productid=7383479) |  | Not available in India | 727.62 | 1455.24 | 2 | 1455.24 | we have it already | 0 | out of stock
J1, J3 | 2 | Conn_01x04_Male | EQ-SM04B-SRSS-TB-W | Connector_JST:JST_SH_BM04B-SRSS-TB_1x04-1MP_P1.00mm_Vertical | Generic connector, single row, 01x04 |  |  | evelta (https://www.evelta.com/jst-4pin-1mm-pitch-male-connector/) | 11.8 | 23.6 | 0 | 0 | Available in toyo connectors | 0
J2, | 1 | Conn_01x02_Female | 2 pin JST XH Series Male Connector | Connector_JST:JST_EH_B2B-EH-A_1x02_P2.50mm_Vertical | Generic connector, single row, 01x02 | -- | -- | ktron (https://www.ktron.in/product/2pin-jst-xh-male-connector/?hsa_acc=6332829093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) | -- | -- | 0 | 0 | Available in toyo connectors | -- | -- | --
Q1, Q2, Q3, Q4, Q5, | 5 | DMN3065LW-7 | DMN3065LW-7 | Package_TO_SOT_SMD:SOT-323_SC-70 | N-MOSFET transistor, drain/gate/source | digikey (https://www.digikey.in/en/products/detail/diodes-incorporated/DMN3065LW-7/4810935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) |  | semikart(digikey) (https://www.semikart.com/product/diodes-incorporated-/DMN3065LW-7/1571201) | 42.893 | 42.893 | 12 | 514.72 |  | 0
R1, | 1 | 10E | 0603SAJ0100T5E | Resistor_SMD:R_0603_1608Metric | Resistor | 10 ohm (₹2.4/10 piece) (https://www.digikey.in/en/products/detail/panasonic-electronic-components/ERJ-2GEJ100X/146733) | 10 ohm (₹1.99/10 piece) (https://www.mouser.in/ProductDetail/YAGEO/RC0402FR-7D10RL?qs=F5EMLAvA7IDtm%252BODDv9POw%3D%3D) | evelta (https://www.evelta.com/10e-5-0603-smd-resistor-royal-ohm-0603saj0100t5e/) | 1.89 | 1.89 | 5 | 5.67 |  | 0.075 | C153363 (https://www.lcsc.com/product-detail/Chip-span-style-background-color-ff0-Resistor-span-Surface-Mount_Ever-Ohms-Tech-TR0603D10R0P0510Z_C153363.html) | 0.075
R4,R21, | 2 | 220E | 0603SAJ0221T5E | Resistor_SMD:R_0603_1608Metric | Resistor |  |  | evelta (https://www.evelta.com/220e-5-0603-smd-resistor-royal-ohm-0603saj0221t5e/) | 1.51 | 3.02 | 10 | 9.44 | got 0402 package | 0 | unavailable
R5, R8, R9, R10, R14, R15,R2, R3, R25 | 9 | 4.7k | RC0402FR-074K7L | Resistor_SMD:R_0402_1005Metric | Resistor |  |  | evelta (https://www.evelta.com/4-7k-1-0402-0-063w-chip-resistor/) | 0.47 | 4.23 | 20 | 5.64 | got 0603 package | 0.3726 | C513719 (https://www.lcsc.com/product-detail/Chip-Resistor-Surface-Mount_YAGEO-AR0603FR-074K7L_C513719.html) | 0.0414
R6, R11, R13, R16, R17, R18, R19, R20, R22, R26 | 10 | 10k | RC0402FR-0710KL | Resistor_SMD:R_0402_1005Metric | Resistor |  |  | evelta (https://www.evelta.com/10k-1-0-063w-0402-chip-resistor/) | 1.18 | 11.8 | 25 | 17.7 | got 0402 package | 0 | out of stock
R7, R12, R23, R24, | 4 | 100E | 0603SAJ0101T5E | Resistor_SMD:R_0603_1608Metric | Resistor |  |  | evelta (https://www.evelta.com/100e-5-0603-smd-resistor-royal-ohm-0603saj0101t5e/) | 1.89 | 7.56 | 10 | 9.44 |  | 0 | unavailable
R27, R28, R29, R30, R31 | 5 | 150E | 0402WGF1500TCE | Resistor_SMD:R_0402_1005Metric | Resistor |  |  | evelta (https://www.evelta.com/150e-1-0402-smd-thick-film-chip-resistor-royal-ohm-0402wgf1500tce/) | 12 | 60 | 10 | 120
SW1, SW2, | 2 | SW_Push | TS342 | TL1015AF160QG:SW_TL1015AF160QG | Push button switch, generic, two pins |  |  | evelta (https://www.evelta.com/tactile-switch-3x4x2mm-smd-2-pin-with-column-button/) | 2.183 | 4.366 | 10 | 21.83 |  | 0 | discontinued
U1, | 1 | BA30BC0FP-E2 | BA30BC0FP-E2 | IPD50P04P4L-11:DPAK228P998X235-3N | 1A 3V LDO |  |  | semikart(mouser) (https://www.semikart.com/product/rohm-semiconductor-/BA30BC0FP-E2/1882817) | 100.78 | 100.78 | 3 | 302.34 |  | 0 | out of stock
U3, | 1 | DRV8833PWPR | DRV8833PWPR | Package_SO:HTSSOP-16_4.4x5mm_P0.65mm | Dual H-Bridge Motor Driver, TSSOP-16 | digikey (https://www.digikey.in/en/products/detail/texas-instruments/DRV8833PW/4251165) | mouser (https://www.mouser.in/ProductDetail/Texas-Instruments/DRV8833PW?qs=biyDIajrTn6dSTURhvWZBQ%3D%3D) | Not available in India | 242 | 242 | 1 | 242.34 |  | 3.4858 | C50506 (https://www.lcsc.com/product-detail/Motor-Driver-ICs_Texas-Instruments-DRV8833PWPR_C50506.html) | 3.4858
U4, | 1 | VL6180XV0NR/1 | VL6180XV0NR/1 | VL6180XV0NR_1:LGA12R75P2X6_280X480X110 | ToF | digikey (https://www.digikey.in/en/products/detail/stmicroelectronics/VL6180XV0NR-1/4854909) | mouser (https://www.google.com/search?q=VL6180XV0NR%2F1+digikay&sourceid=chrome&ie=UTF-8) | tanotis (https://www.tanotis.com/products/stmicroelectronics-vl6180xv0nr-1-proximity-module-digital-lga-12) | 648 | 648 | 1 | 648 |  | 3.2063 | C2688732 (https://www.lcsc.com/product-detail/Ambient-Light-Sensors_STMicroelectronics-VL6180XV0NR-1_C2688732.html) | 3.2063
U5, | 1 | MPU-6500 | MPU-6500 | MPU-6500:QFN40P300X300X95-25N | IMU | digikey (https://www.digikey.in/en/products/detail/tdk-invensense/MPU-6500/4385413?cur=INR&lang=en&productid=4385413) | mouser (https://www.mouser.in/ProductDetail/TDK-InvenSense/MPU-6500?qs=u4fy%2FsgLU9PiIOIlWOSPhQ%3D%3D) | Not available in India (from module) | 727.89 | 727.89 | 1 | 727.89 |  | 3.5651 | C50278 (https://www.lcsc.com/product-detail/Attitude-Sensor-Gyroscope_TDK-InvenSense-MPU6500_C50278.html) | 3.5651
U6, | 1 | STM32F405RGT6 | STM32F405RGT6 | Package_QFP:LQFP-64_10x10mm_P0.5mm | ARM Cortex-M4 MCU, 1024KB flash, 128KB RAM, 168MHz, 1.8-3.6V, 51 GPIO, LQFP-64 | digikey (https://www.digikey.in/en/products/detail/stmicroelectronics/STM32F405RGT6/2754208) | mouser (https://www.mouser.in/ProductDetail/STMicroelectronics/STM32F405RGT6?qs=Z8%252BeY1k3TIKgj7QWsYGpQw%3D%3D) | Not available in India |  | 0 |  | 0 |  | 10.1327 | C15742 (https://www.lcsc.com/product-detail/Microcontroller-Units-MCUs-MPUs-SOCs_STMicroelectronics-STM32F405RGT6_C15742.html) | 10.1327
Y1, | 1 | 25Mhz | EC-9631 | Crystal:Crystal_SMD_3225-4Pin_3.2x2.5mm | Four pin crystal, GND on pins 2 and 4 |  |  | electronicscomp (https://www.electronicscomp.com/ysx321sl-25mhz-20pf-10ppm-4pins-smd-smt-metal-surface-quartz-crystal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) | 34.69 | 34.69 | 10 | 208.14 |  | 0.8782 | C295525 (https://www.lcsc.com/product-detail/Oscillators_TAITIEN-Elec-OXETGLJANF-25MHZ_C295525.html) | 0.8782
Y2, | 1 | 32.768kHz | X3215-32.768K-12.5 | ABS07-32:XTAL_ABS07-32.768KHZ-T | Two pin crystal | assign footprint |  | evelta (https://www.evelta.com/32-768-khz-12-5-pf-tuning-fork-quartz-crystal-smd-3-2x1-5x0-8mm-2pad/) | 9.44 | 9.44 | 3 | 28.32 |  | 0.1737 | C93228 (https://www.lcsc.com/product-detail/Crystals_KDS-Daishinku-DT-38-32-768KHz_C93228.html) | 0.1737
Number of SMD components = | 103
 |  |  |  |  |  |  |  |  |  |  | TOTAL | 5681.85
 | 99

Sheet: mushak_pcb
di
 |  |  |  | MUSHAK BILL OF MATERIALS
Ref | Quantity | Value | Comp name | Footprint | Description | Indian Vendor (best price) | Vendor (Digikey) | Vendor (Mouser) | LCSC | Best Buy (₹) /peice | Purchase Qty | Cost per build (₹) | Overall cost (₹) | Comments
A1, A2, A3, A4, | 4 | SFH_3015_FA | SFH_3015_FA | SFH_3015_FA:XDCR_SFH_3015_FA | Photo-Transistor | Not available in India | SFH_3015_FA (₹49.86/10piece) (https://www.digikey.in/en/products/detail/ams-osram-usa-inc/SFH-3015-FA/2415039) | SFH_3015_FA (₹40.86/10piece) (https://www.mouser.in/ProductDetail/ams-OSRAM/SFH-3015-FA?qs=JdgXXoipWqUDlNTnoH77ZA%3D%3D) | out of stock | 59.93 | 10 | 239.72 | 498.58 | Not available on Indian sites
BZ1, | 1 | Buzzer | Buzzer | SMT-0440-T-R:XDCR_SMT-0440-T-R | Buzzer, polarized | Not available in India | digikey (https://www.digikey.in/en/products/detail/pui-audio-inc/SMT-0440-T-R/5113608) | mouser (https://www.mouser.in/ProductDetail/PUI-Audio/SMT-0440-T-R?qs=7PCaVhlmG1oC7sD2lJM0%2Fg%3D%3D) | discontinued | 247.69 | 2 | 247.69 | 495.38 | SMD version not available in India
C1, C2, C27, | 3 | 2.2uF | C | Capacitor_SMD:C_0402_1005Metric | Unpolarized capacitor | evelta (https://www.evelta.com/2-2uf-10v-10-x5r-0603-ceramic-capacitor/) | 2.2uF_0402 (₹18.46/10piece) (https://www.digikey.in/en/products/detail/tdk-corporation/C1005JB1A225K050BC/3948140) | 2.2uF_0402 (₹11.69/10 piece) (https://www.mouser.in/ProductDetail/Kyocera-AVX/CM05X7S225M06AH065?qs=A6eO%252BMLsxmS301H7ZRkNqA%3D%3D) | C417153_$0.09 (https://www.lcsc.com/product-detail/Multilayer-Ceramic-Capacitors-MLCC-span-style-background-color-ff0-SMD-span-SMT_Murata-Electronics-GRM155R61C225ME11D_C417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) | 2.12 | 10 | 6.36 | 12.74 | 0603 package available
C3, C4, C30, C32, C33, | 5 | 0.1uF | C | Capacitor_SMD:C_0402_1005Metric | Unpolarized capacitor | evelta (https://www.evelta.com/100nf-50v-10-x7r-0402-ceramic-capacitor/) | 0.1uF_0402 (₹2.32/10piece) (https://www.digikey.in/en/products/detail/walsin-technology-corporation/0402B104K160CT/6707534) | 0.1uF_0402 (₹3.34/10 piece) (https://www.mouser.in/ProductDetail/Kyocera-AVX/04023C104KAT4A?qs=XLNwXgtzMM%2FjcUD%2FzDf3Ww%3D%3D) | discontinued | 49 | 50 | 49 | 49 | pack of 50
C8, C13, | 2 | 47uF | C | Capacitor_SMD:C_0402_1005Metric | Unpolarized capacitor | evelta (https://www.evelta.com/47uf-6-3v-20-x5r-0805-ceramic-capacitor/) | 47uf_0603 (₹30.84/10 piece) (https://www.digikey.in/en/products/detail/murata-electronics/GRM188R60G476ME15D/5877409) | 47uF_0603 (₹36.97/10 piece) (https://www.mouser.in/ProductDetail/Kyocera-AVX/06034W476MAT2A?qs=Znm5pLBrcAKygBdcRiKAig%3D%3D) | 0402 not found | 7.08 | 10 | 14.16 | 42.48
C11, C15, | 2 | 20pF | C | Capacitor_SMD:C_0402_1005Metric | Unpolarized capacitor | evelta (https://www.evelta.com/22-pf-50v-0402-smd-multi-layer-ceramic-capacitor-0402n220j500ct-walsin/) |  | 20 pF (12.41/10 piece) (https://www.mouser.in/ProductDetail/Kyocera-AVX/04025A200JAT2A?qs=HeiVa0IqVQ2m4eBQNX5O9Q%3D%3D) | discontinued | 3.96 | 10 | 7.92 | 20.2 | got 22pF instead of 20pF
C12, C19, | 2 | 1uF | C | Capacitor_SMD:C_0402_1005Metric | Unpolarized capacitor | evelta (https://www.evelta.com/1-uf-50v-10-0603-x5r-mlcc-multilayer-ceramic-capacitor-smd-cc0603krx5r9bb105/) |  |  |  | 7.08 | 10 | 14.16 | 35.4 | got 0603 package
C20, C21, | 2 | 12.5pF | C | Capacitor_SMD:C_0402_1005Metric | Unpolarized capacitor | evelta (https://www.evelta.com/12-pf-50v-0402-smd-multilayer-ceramic-capacitors-cc0402jrnpo9bn120-yageo/) |  |  |  | 2.5 | 10 | 5 | 12.51 | got 12 pF instead of 12.5pF
C22, C24, C28, C18, | 4 | 10uF | C | Capacitor_SMD:C_0402_1005Metric | Unpolarized capacitor | evelta (https://www.evelta.com/10uf-6-3v-20-x5r-0603-capacitor/) | 10uF_0402 (₹10.07/10 piece) (https://www.digikey.in/en/products/detail/samsung-electro-mechanics/CL05X106MR5NUNC/5961263) |  |  | 3.54 | 10 | 14.16 | 21.24 | got 0603 package
C7, C9, C10, C14, C16, , C23, C25, | 7 | 100nF | C | Capacitor_SMD:C_0402_1005Metric | Unpolarized capacitor | 100nF_0402 (₹1.78/40 piece) (https://robu.in/product/100nf-0603-surface-mount-multilayer-ceramic-capacitor-pack-of-40/) | too costly | 100nF_0402 (₹2.86/10 piece) (https://www.mouser.in/ProductDetail/TDK/C1005X7R1C104K050BC?qs=NRhsANhppD%252BhAGOapA8QKQ%3D%3D) |  | 1.78 | 40 | 12.46 | 71.2
C26, C17, | 2 | 10nF | C | Capacitor_SMD:C_0402_1005Metric | Unpolarized capacitor | 10nF_0603 (₹2/50 piece) (https://robu.in/product/10nf-0603-surface-mount-multilayer-ceramic-capacitor-pack-of-50/) | 10nF_0402 (₹8.79/10 piece) (https://www.digikey.in/en/products/detail/kemet/C0402C103K5RECAUTO/8646477) | 10nF_0402 (₹13.28/10 piece) (https://www.mouser.in/ProductDetail/Vishay-Vitramon/VJ0402Y103KXAAC?qs=e%2F7vlcXyL81c3K8Dz3L1zQ%3D%3D) |  | 2 | 50 | 4 | 100
C29, | 1 | 4.7uF | C | Capacitor_SMD:C_0402_1005Metric | Unpolarized capacitor | 4.7uF_0603 (₹1.8/10 piece) (https://www.electronicscomp.com/4.7uf-4700nf-50v-smd-capacitor-0603-package?search=4.7uF) | 4.7_0402 (₹21.97/10 piece) (https://www.digikey.in/en/products/detail/tdk-corporation/C1005JB0G475M050BB/3948109) | 4.7uF_0402 (₹19.16/10 piece) (https://www.mouser.in/ProductDetail/Kyocera-AVX/CM05X5R475M25AH?qs=MyNHzdoqoQJvFdZaEuclBg%3D%3D) |  | 1.8 | 10 | 1.8 | 18
C31, | 1 | 0.01uF | C | Capacitor_SMD:C_0402_1005Metric | Unpolarized capacitor | 0.01uF_0603 (₹1.8/10 piece) (https://www.electronicscomp.com/10nf-50v-smd-capacitor-0603-package?search=0.01uF) | (0.01uF (₹10.31/10 piece) (https://www.digikey.in/en/products/detail/taiyo-yuden/HMK105B7103MVHFE/11687499) | 0.01uF (₹11.93/10 piece) (https://www.mouser.in/ProductDetail/Taiyo-Yuden/HMR105B7103MV-F?qs=DPoM0jnrROWTfrErHcoxtg%3D%3D) |  | 1.8 | 10 | 1.8 | 18
D1, D6, | 2 | LED | LED | LED_SMD:LED_0402_1005Metric | Light emitting diode |  |  |  |  |  |  | 0 | 0
D2, D3, D4, D5, | 4 | SFH_4045N | SFH_4045N | SFH_4045N:LED_SFH_4045N | IR LED Transmitter |  | SFH_4045N (₹51.14) (https://www.digikey.in/en/products/detail/ams-osram-usa-inc/SFH-4045N/4360733) | SFH_4045N (₹52.47) (https://www.mouser.in/ProductDetail/ams-OSRAM/SFH-4045N?qs=9EKcitwk7VRzbAsL4%252B52Qg%3D%3D) |  |  |  | 0 | 0
FB1, | 1 | 120R | FerriteBead_Small | Inductor_SMD:L_0805_2012Metric | Ferrite bead, small symbol |  |  |  |  |  |  | 0 | 0
IC1, IC2, | 2 | AS5600-ASOT | AS5600-ASOT | AS5600-ASOT:SOIC127P600X175-8N | Magnetic Encoder |  | AS5600-ASOT (₹269.26) (https://www.digikey.in/en/products/detail/ams-osram/AS5600-ASOT/4914338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) | AS5600-ASOT (₹267.92) (https://www.mouser.in/ProductDetail/ams/AS5600-ASOT?qs=KTMMzrZdriGJpjhsnAEYBA%3D%3D) |  |  |  | 0 | 0
J1, | 1 | Conn_01x04_Male | Conn_01x04_Male | Connector_JST:JST_SH_SM04B-SRSS-TB_1x04-1MP_P1.00mm_Horizontal | Serial Wire connector |  |  |  |  |  |  | 0 | 0
J2, | 1 | Conn_01x02_Female | Conn_01x02_Female | Connector_JST:JST_EH_B2B-EH-A_1x02_P2.50mm_Vertical | Power connector |  |  |  |  |  |  | 0 | 0
Q1, Q2, Q3, Q4, Q5, | 5 | DMN3065LW-7 | Q_NMOS_DGS | Package_TO_SOT_SMD:SOT-323_SC-70 | N-MOSFET transistor, drain/gate/source |  |  |  |  |  |  | 0 | 0
R1, | 1 | 10ohm | R | Resistor_SMD:R_0402_1005Metric | Resistor | 10 ohm (₹12) (https://www.electronicscomp.com/10-ohm-0402-package-1-16w-smd-resistor-1-percent-tolerance-20-pieces-pack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) | 10 ohm (₹2.4/10 piece) (https://www.digikey.in/en/products/detail/panasonic-electronic-components/ERJ-2GEJ100X/146733) | 10 ohm (₹1.99/10 piece) (https://www.mouser.in/ProductDetail/YAGEO/RC0402FR-7D10RL?qs=F5EMLAvA7IDtm%252BODDv9POw%3D%3D) |  | 12 |  | 12 | 0
R2, R3, | 2 | 5k | R | Resistor_SMD:R_0402_1005Metric | Resistor |  | 5k ohm (₹1.28/10 piece) (https://www.digikey.in/en/products/detail/yageo/RC0402FR-075KL/5917711) | 5.1k ohm (₹1.99/10 piece) (https://www.mouser.in/ProductDetail/Bourns/CR0402-FX-5101GLF?qs=ePR1ZvdkOKImkuXR%2F%2FtvtA%3D%3D) |  |  |  | 0 | 0
R4, R21, | 2 | 220 ohm | R | Resistor_SMD:R_0402_1005Metric | Resistor | 220 ohm_0402 (₹1.67/20 piece) (https://www.electronicscomp.com/220-ohm-0402-package-1-16w-smd-resistor-1-percent-tolerance-20-pieces-pack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) |  | 220 ohm (₹45.87/10 piece) (https://www.digikey.in/en/products/detail/yageo/RC0402FR-075KL/5917711) |  | 1.67 | 20 | 3.34 | 33.4
R5, R6, R8, R9, R10, R11, R13, R14, R15, R22, | 10 | 4.7k | R | Resistor_SMD:R_0402_1005Metric | Resistor | 4.7k ohm (₹0.39/100 piece) (https://robu.in/product/4-7k-ohm-1-4w-0603-surface-mount-chip-resistor-pack-of-100/) | 4.7k ohm (₹2.56/10 piece) (https://www.digikey.in/en/products/detail/vishay-dale/CRCW04024K70JNED/1177584) | 4.7k ohm (₹0.72/10 piece) (https://www.mouser.in/ProductDetail/Bourns/CR0402-JW-472GLF?qs=6eDBzTnH09kw5SBfs1pxfg%3D%3D) |  | 0.39 | 100 | 3.9 | 39
R7, R12, R23, R24, | 4 | 100 ohm | R | Resistor_SMD:R_0402_1005Metric | Resistor | 100 ohm_0603 (₹0.45/100 piece) (https://robu.in/product/100-ohm-1-4w-0603-surface-mount-chip-resistor-pack-of-100/) | 100 ohm (₹1.2/10 piece) (https://www.digikey.in/en/products/detail/stackpole-electronics-inc/RMCF0402FT100R/1761807) | 100 ohm (₹24.88/10 piece) (https://www.mouser.in/ProductDetail/Panasonic/ERJ-H2RD1000X?qs=eP2BKZSCXI5g%2FeXWJadQHQ%3D%3D) |  | 0.45 | 100 | 1.8 | 45
R16, R17, R18, R19, R20, | 5 | 10k | R | Resistor_SMD:R_0402_1005Metric | Resistor | 10k ohm(₹0.6/20 piece) (https://www.electronicscomp.com/10k-ohm-0402-package-1-16w-smd-resistor-1-percent-tolerance-20-pieces-pack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) | 10k ohm (₹1.2/10 piece) (https://www.digikey.in/en/products/detail/stackpole-electronics-inc/RMCF0402FT10K0/1761433) | out of stock |  | 0.6 | 20 | 3 | 12
R25, | 1 | 47k | R | Resistor_SMD:R_0402_1005Metric | Resistor | 47k ohm (₹0.6/20 piece) (https://www.electronicscomp.com/47k-ohm-0402-package-1-16w-smd-resistor-1-percent-tolerance-20-pieces-pack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) | 47k ohm (₹0.96/10 piece) (https://www.digikey.in/en/products/detail/stackpole-electronics-inc/RMCF0402JT47K0/1712463) | 47k ohm (₹34.74/10 piece) (https://www.mouser.in/ProductDetail/TE-Connectivity-Holsworthy/CPF-A-0402B47KE1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) |  | 0.6 | 20 | 0.6 | 12
SW1, SW2, | 2 | SW_Push | SW_Push | Button_Switch_SMD:SW_SPST_CK_RS282G05A3 | Push button switch, generic, two pins |  |  | sw_push H6.0mm (165.36) (https://www.mouser.in/ProductDetail/Panasonic/ESB-33134?qs=sGAEpiMZZMsqIr59i2oRcvgdFGkouwgFryxCjVp14Tk%3D) |  |  |  | 0 | 0
U2, | 1 | TLV1117LV30DCYT | AMS1117-3.3 | SOT230P700X180-4N:SOT230P700X180-4N | 1A Low Dropout regulator, positive, 3.3V fixed output, SOT-223 | AMS-1117-3.3 (₹13) (https://www.electronicscomp.com/ams1117-3.3v-voltage-regulator-smd-sot-23-package-india?search=AMS1117-3.3) |  |  |  | 13 |  | 13 | 0
U3, | 1 | DRV8833PW | DRV8833PW | Package_SO:TSSOP-16_4.4x5mm_P0.65mm | Dual H-Bridge Motor Driver, TSSOP-16 | DRV8833 (₹99) (https://robu.in/product/drv8833-2-channel-dc-motor-driver-module/) | out of stock | out of stock |  | 99 |  | 99 | 0
U4, | 1 | VL6180XV0NR/1 | VL6180XV0NR{slash}1 | VL6180XV0NR_1:LGA12R75P2X6_280X480X110 | ToF Sensor | VL6180X (₹689) (https://robu.in/product/dfrobot-fermion-vl6180x-tof-distance-ranging-sensor-breakout/) | VL6180XV0NR/1 (₹415.48) (https://www.digikey.in/en/products/detail/stmicroelectronics/VL6180XV0NR-1/4854909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) | VL6180XV0NR/1 (₹413.4) (https://www.mouser.in/ProductDetail/STMicroelectronics/VL6180XV0NR-1?qs=bOHV6dImh3MAxp12geXi0Q%3D%3D) |  | 689 |  | 689 | 0
U5, | 1 | MPU-6500 | MPU-6500 | MPU-6500:QFN40P300X300X95-25N | Motion Processing Unit | mpu 6500 (₹629) (https://robu.in/product/mpu6500-gyroscope-accelerometer-digital-motion-processor-dmp-6-axis-motion-sensor-with-i2c-spi-interface/) | mpu 6500 (₹727.89) (https://www.digikey.in/en/products/detail/tdk-invensense/MPU-6500/4385412?s=N4IgTCBcDaILYAcCuA2ArABgyAugXyA) | out of stock |  | 629 |  | 629 | 0
U6, | 1 | STM32F405RGTx | STM32F405RGTx | Package_QFP:LQFP-64_10x10mm_P0.5mm | ARM Cortex-M4 MCU, 1024KB flash, 128KB RAM, 168MHz, 1.8-3.6V, 51 GPIO, LQFP-64 |  | out of stock | STM32F405RGT7TR (₹1347.53) (https://www.mouser.in/ProductDetail/STMicroelectronics/STM32F405RGT7TR?qs=4ccVDqXDOrlkg5BcAUdo%252BA%3D%3D) |  |  |  | 0 | 0
Y1, | 1 | 25Mhz | Crystal_GND24 | Crystal:Crystal_SMD_3225-4Pin_3.2x2.5mm | Four pin crystal, GND on pins 2 and 4 | 25MHz (₹39) (https://robu.in/product/ysx531sl-25mhz-20pf-10ppm-4pad-smd-smt-crystal/) | 25MHz (₹67.12) (https://www.digikey.in/en/products/detail/txc-corporation/8Q-25-000MDDV-T/13402618) | 25MHz (₹42.93) (https://www.mouser.in/ProductDetail/ABRACON/ABM8-25.000MHZ-D2X-T?qs=XeJtXLiO41RuPiM7CXbPRQ%3D%3D) |  | 39 |  | 39 | 0
Y2, | 1 | 32.769kHz | Crystal | ABS07-32:XTAL_ABS07-32.768KHZ-T | Two pin crystal | 32.768kHz (₹339) (https://robu.in/product/abs07-32-768khz-t-crystal/) | 32.768kHz (₹144.62) (https://www.digikey.in/en/products/detail/abracon-llc/ABS05-32-768KHZ-X-T5/15907277) | 32.768kHz (₹57.24) (https://www.mouser.in/ProductDetail/ABRACON/ABS07-32.768KHZ-T?qs=3SpAxaLJ01g8GJWeO3sA3Q%3D%3D) |  | 339 |  | 339 | 0

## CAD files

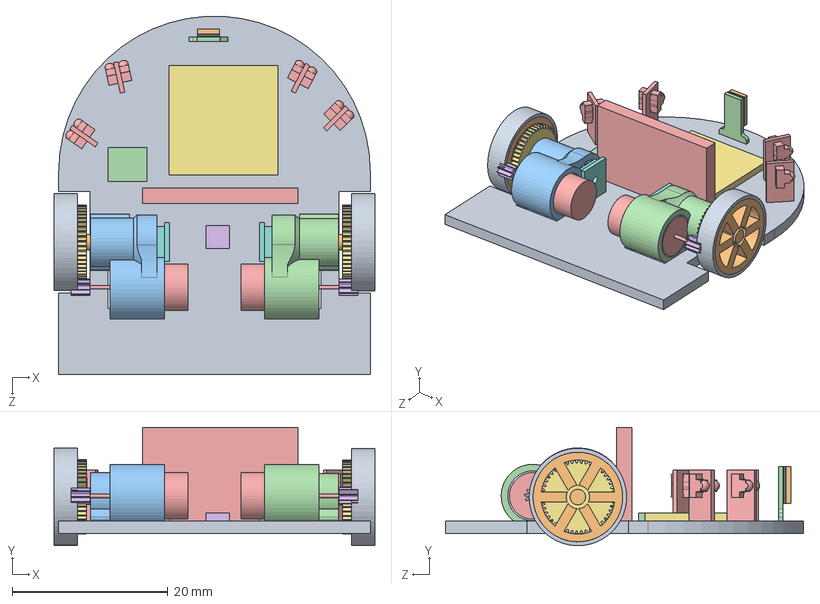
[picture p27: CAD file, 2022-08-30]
cad_design/Final_Assembly/Final_New.SLDASM
41.2 x 15.2 x 46.0 mm
mushak_chassis
mushak_shaft x 2
New_mount_2
New_mount_R_2
mushak_motor x 2
SpurPinion x 2
SpurGear (1) x 2
Board_Encoder.step x 2
mushak_wheels x 2
mushak_rims x 2
single row radial ball bearing_is x 4
drv8833
lipo_battery
mpu6500
stm32f407
_______1.step
_______1-0.step
_______1-1.step
_______1-2.step
board-tof v2.step
photo-set v4 (1) x 4

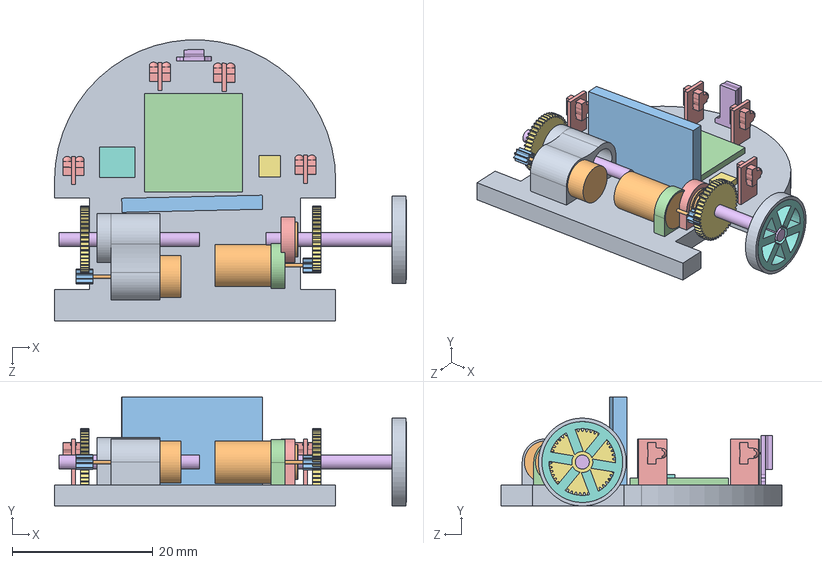
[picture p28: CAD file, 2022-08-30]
cad_design/Extras/Assem7.SLDASM
50.1 x 15.5 x 40.0 mm
mushak_chassis
mushak_motor x 2
SpurPinion x 2
mushak_motor_base
mushak_shaft_base x 2
mushak_shaft x 2
SpurGear (1) x 2
mushak_rims
mushak_wheels
instrument ball bearing_68_am
mushak_battery
mushak_stm
photo-set v4 (1) x 4
tof-set v2
mpu6500
drv8833
New_mount

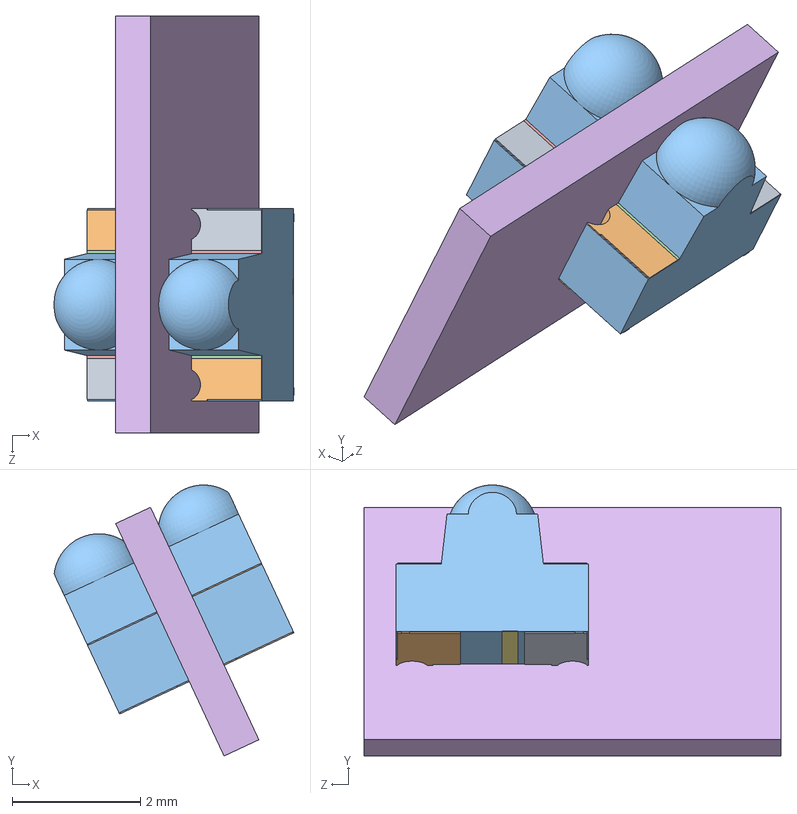
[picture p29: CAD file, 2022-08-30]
cad_design/Extras/Assem24.SLDASM
3.74 x 4.23 x 6.50 mm
SFH 4045N--3DModel-STEP-56544 v1.step x 2
SFH 4045N--3DModel-STEP-56544 v1-0.step x 2
SFH 4045N--3DModel-STEP-56544 v1-1.step x 2
SFH 4045N--3DModel-STEP-56544 v1-2.step x 2
SFH 4045N--3DModel-STEP-56544 v1-3.step x 2
board-photo v2.step
SFH 4045N--3DModel-STEP-56544 v1-4.step x 2

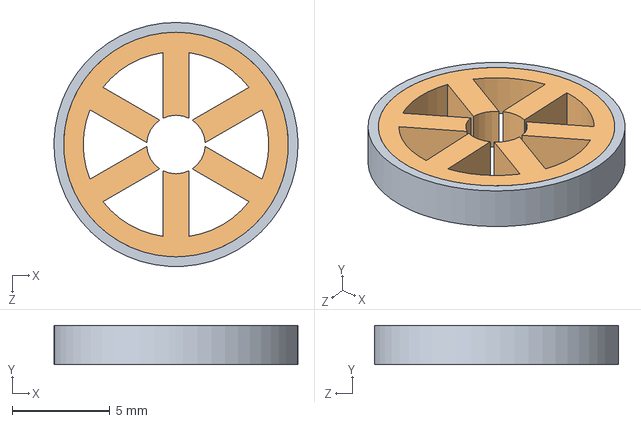
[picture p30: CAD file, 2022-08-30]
cad_design/Final_Assembly/mushak_Wheel.SLDASM
12.5 x 2.00 x 12.5 mm
mushak_wheels
mushak_rims

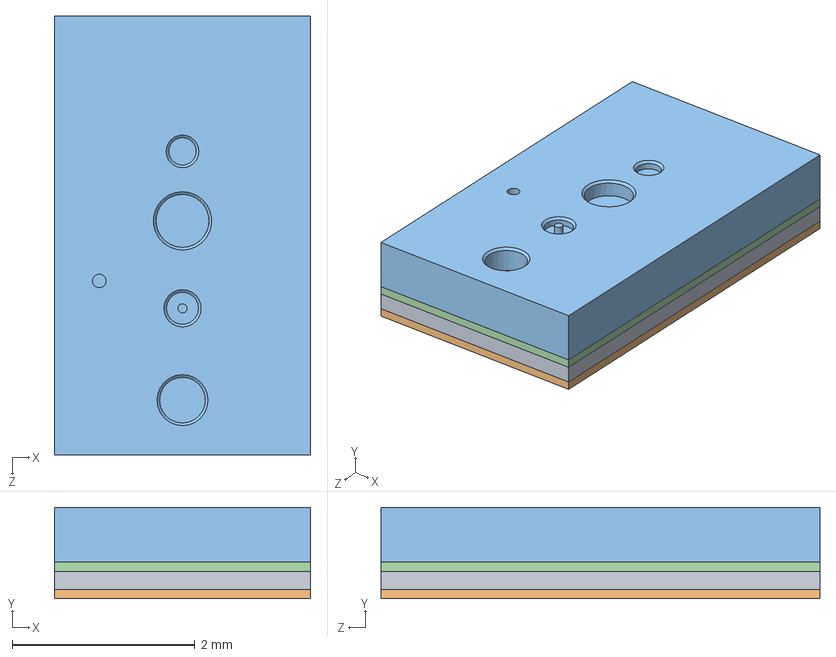
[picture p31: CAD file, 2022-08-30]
cad_design/Extras/tof-set v2.SLDASM
2.80 x 1.00 x 4.80 mm
_______1.step
_______1-0.step
_______1-1.step
_______1-2.step

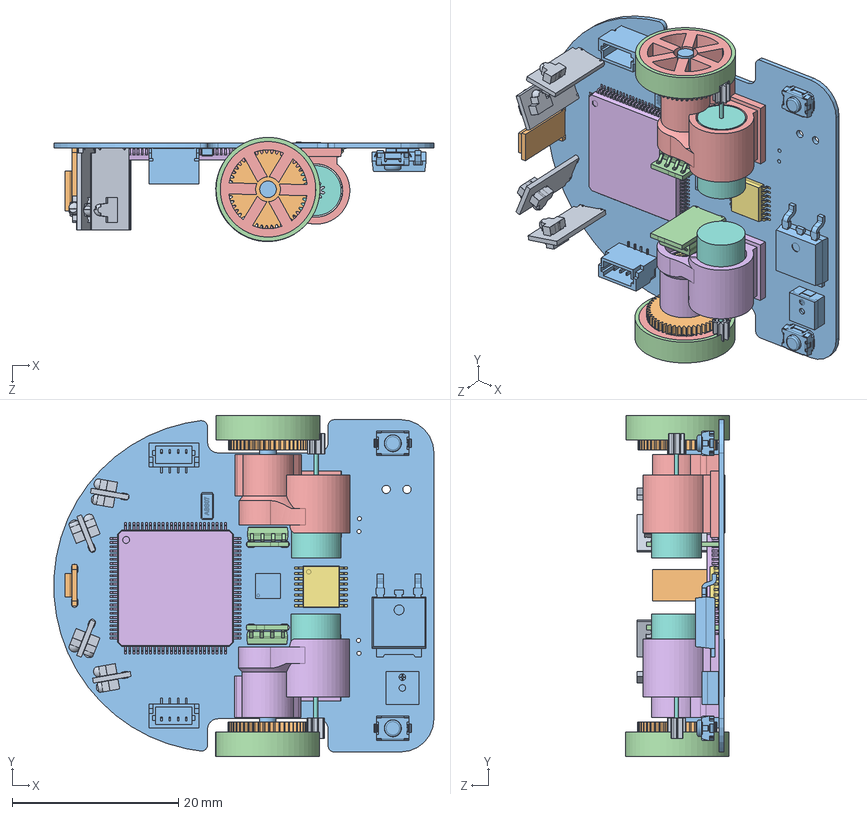
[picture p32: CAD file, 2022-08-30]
cad_design/Final_Assembly/PCB_Assem.SLDASM
45.7 x 41.1 x 12.5 mm
IR_Sensor_Mushak v1.step x 4
TOF_Sensor_Mushak v1.step
mushak_pcb_base v0.step
mushak_pcb v1.step x 2
New_mount_R_2
New_mount_2
single row radial ball bearing_is x 4
mushak_motor x 2
SpurPinion x 2
SpurGear (1) x 2
mushak_shaft x 2
mushak_wheels x 2
mushak_rims x 2
STM32.step
DRV8833.step

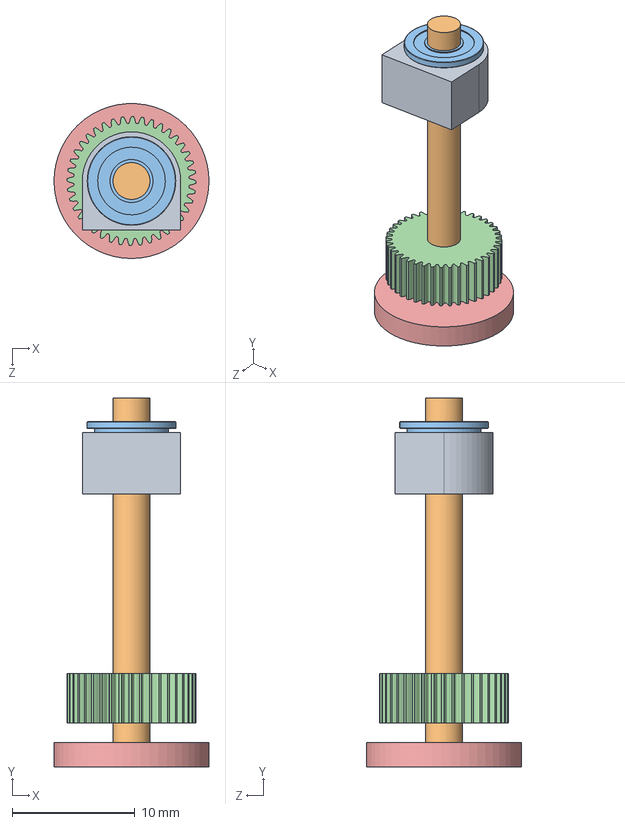
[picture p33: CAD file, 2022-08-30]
cad_design/Extras/final.SLDASM
12.6 x 30.0 x 12.6 mm
base_motor
shaft
MF63zz 3x6x2.5mm Flanged Bearing.step
SpurGear
wheels

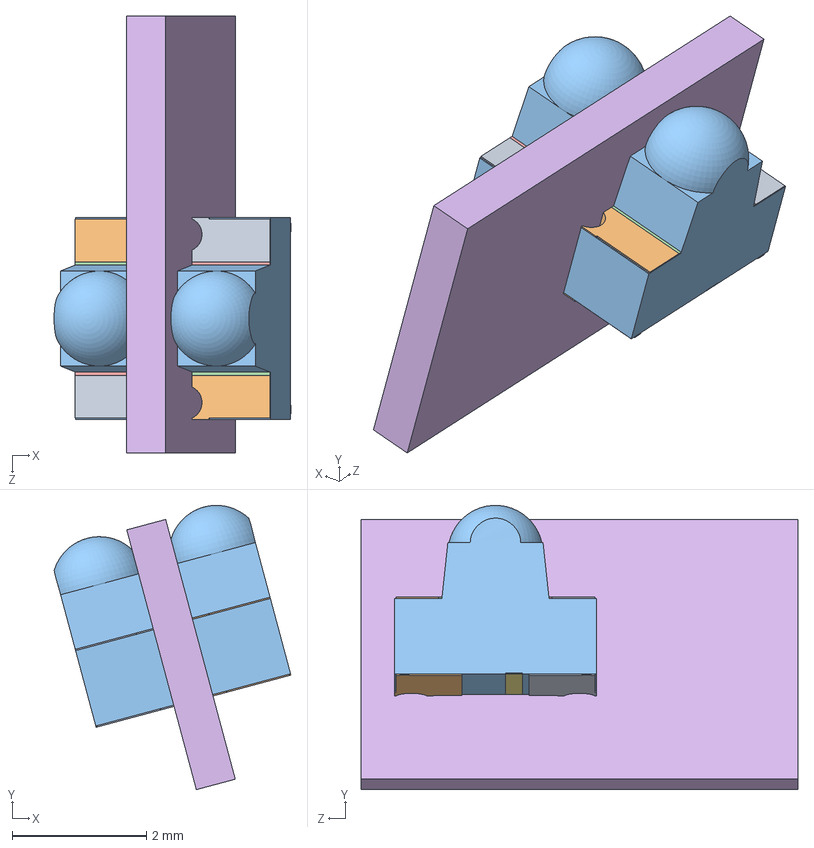
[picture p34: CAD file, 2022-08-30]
cad_design/Extras/photo-set v4 (1).SLDASM
3.52 x 4.23 x 6.50 mm
SFH 4045N--3DModel-STEP-56544 v1.step x 2
SFH 4045N--3DModel-STEP-56544 v1-0.step x 2
SFH 4045N--3DModel-STEP-56544 v1-1.step x 2
SFH 4045N--3DModel-STEP-56544 v1-2.step x 2
SFH 4045N--3DModel-STEP-56544 v1-3.step x 2
board-photo v2.step
SFH 4045N--3DModel-STEP-56544 v1-4.step x 2

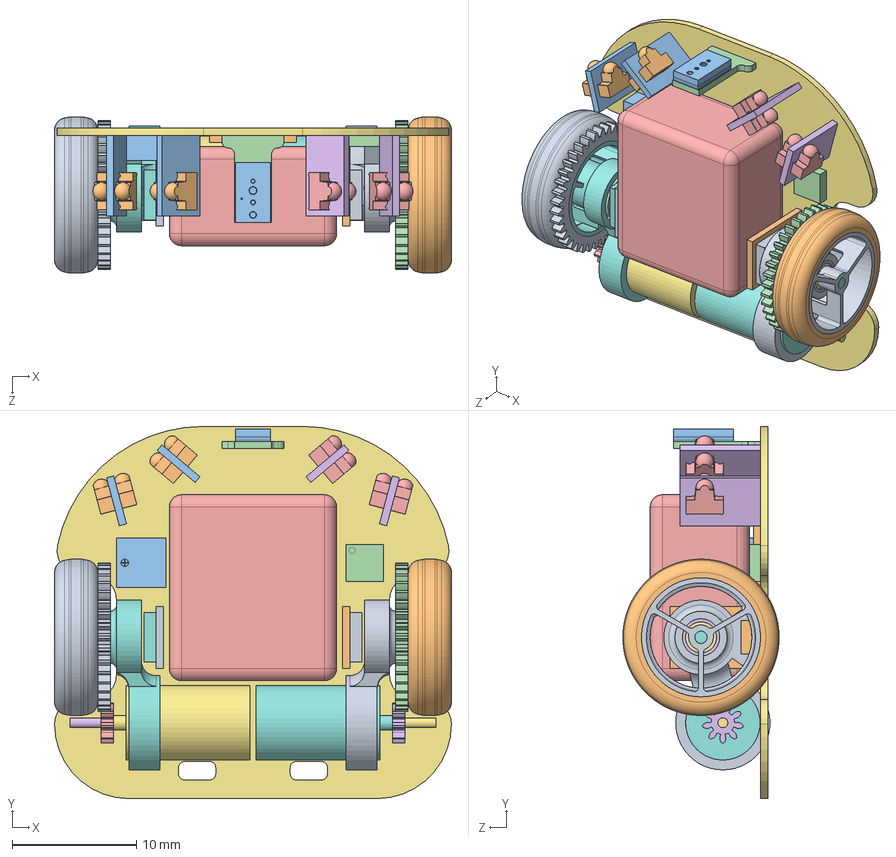
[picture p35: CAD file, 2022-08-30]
cad_design/Final_Assembly/KERISE v5 mouse v128.SLDASM
32.0 x 30.0 x 12.6 mm
Spur Gear (38 teeth).step
コンポーネント1.step x 2
bearing_1-3-1-0.step
bearing_1-3-1-1.step
bearing_1-3-1_1-2.step
bearing_1-3-1_1-3.step
shaft-wheel.step
wheel.step
tire.step
magnet-mounter.step
magnet.step
iron-spacer.step
Spur Gear (9 teeth).step
コンポーネント1_1.step
motor-4.step
Encoder.step
board-encoder-5.step
SFH 4045N--3DModel-STEP-56544.step x 4
board-photo.step x 2
Spur Gear (38 teeth)(ミラー) (1).step
コンポーネント1(ミラー) (1).step x 2
bearing_1-3-1 v1(ミラー) (1)-6.step x 2
bearing_1-3-1 v1(ミラー) (1)-7.step x 2
shaft-wheel v3(ミラー) (1).step
wheel v5(ミラー) (1).step
tire v2(ミラー) (1).step
magnet-mounter v4(ミラー) (1).step
magnet v2(ミラー) (1).step
iron-spacer v3(ミラー) (1).step
Spur Gear (9 teeth)(ミラー) (1).step
コンポーネント1(ミラー).step
motor v3(ミラー)-8.step
Encoder v2(ミラー) (1).step
board-encoder v5(ミラー)-9.step
コンポーネント1_2.step
board-tof.step
SFH 4045N--3DModel-STEP-56544 v1(ミラー).step x 4
board-photo v2(ミラー).step x 2
board v7.step
mounter.step
mounter v36(ミラー) (1).step
MCU.step
SMT-0440.step
IMU.step x 2
battery.step

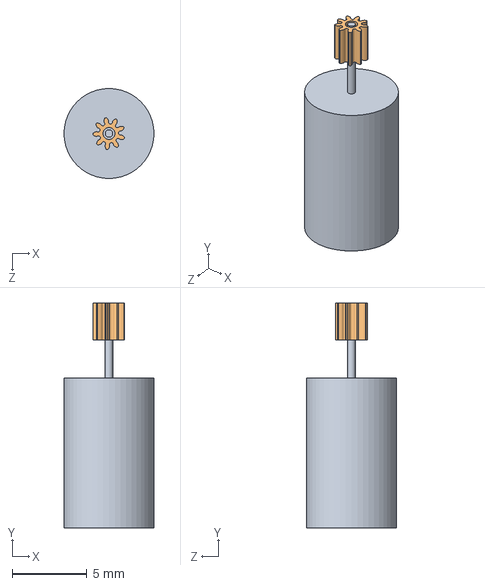
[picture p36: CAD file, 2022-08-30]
cad_design/Final_Assembly/Assem2.SLDASM
6.00 x 15.0 x 6.00 mm
mushak_motor
SpurPinion

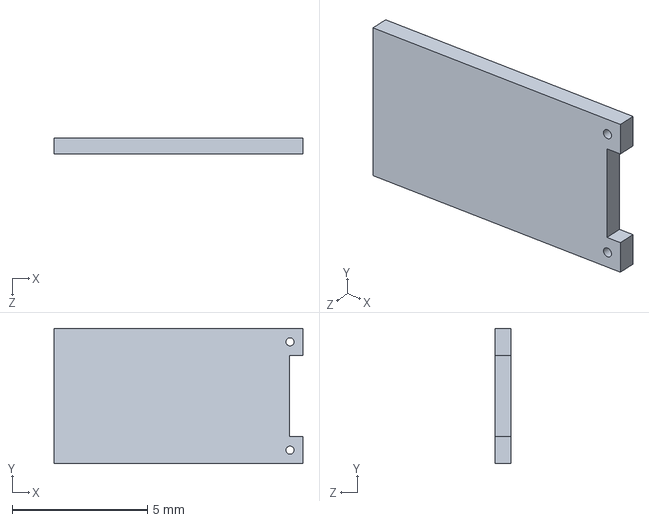
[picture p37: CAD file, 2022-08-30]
cad_design/Extras/Encoder_Base.SLDPRT
9.20 x 5.00 x 0.6 mm

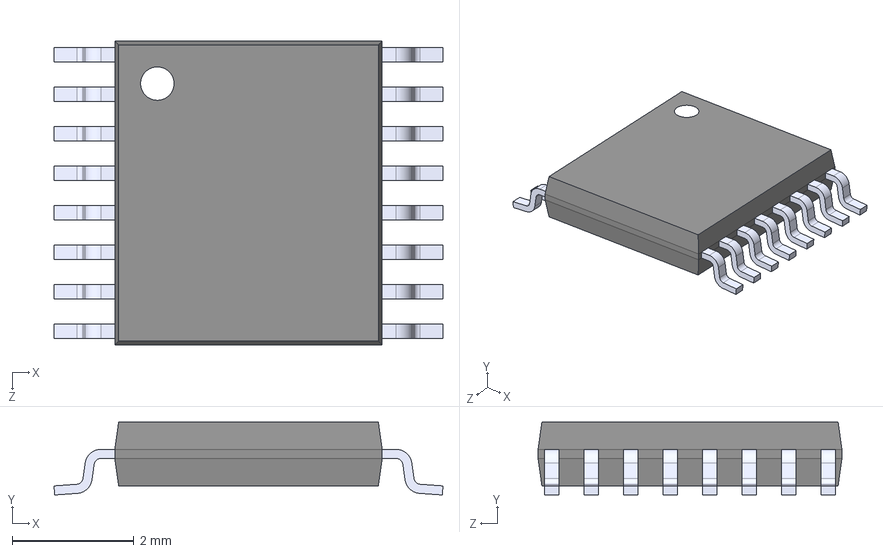
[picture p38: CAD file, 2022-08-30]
cad_design/Step_Files/DRV8833.step
6.40 x 1.20 x 5.00 mm

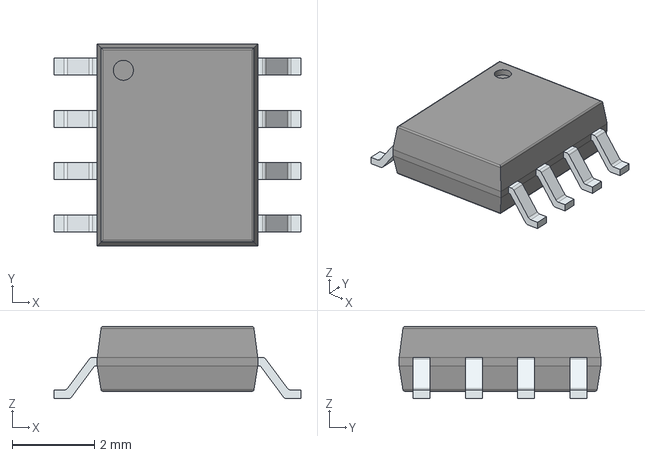
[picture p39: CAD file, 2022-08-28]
pcb_design/3d_models/AS5600/AS5600.stp
6.00 x 4.90 x 1.75 mm
PinsArrayLR

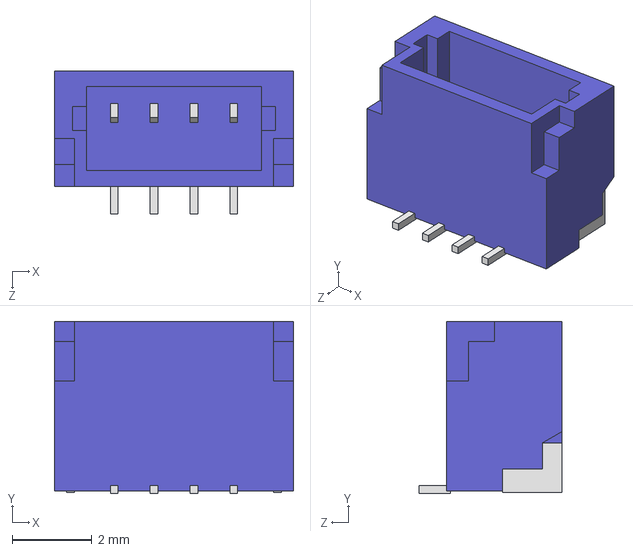
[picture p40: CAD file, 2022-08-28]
pcb_design/3d_models/JST_Connector/BM04B-SRSS-TB.STEP
6.00 x 4.32 x 3.60 mm

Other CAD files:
pcb_design/3d_models/SFH/photo-set v4 (1).STEP
pcb_design/3d_models/VL6180x/tof-set v2.STEP
pcb_design/component_libraries/ABS07-32.768KHZ-T/ABS07-32.768KHZ-T.step
pcb_design/component_libraries/AMS1117-3.3/AMS1117-3.3.step
cad_design/Extras/New_mount.SLDPRT
cad_design/Extras/New_mount_2.SLDPRT
cad_design/Extras/New_mount_2_Hole.SLDPRT
cad_design/Extras/New_mount_R.SLDPRT
cad_design/Extras/New_mount_R_2.SLDPRT
cad_design/Extras/base_motor.SLDPRT
cad_design/Extras/drv8833.SLDPRT
cad_design/Extras/lipo_battery.SLDPRT
cad_design/Extras/motor.SLDPRT
cad_design/Extras/mpu6500.SLDPRT
cad_design/Extras/sensors_placement.SLDPRT
cad_design/Extras/stm32f407.SLDPRT
cad_design/Extras/wheels.SLDPRT
cad_design/Final_Assembly/Board_Encoder.step.SLDPRT
cad_design/Final_Assembly/New_mount_2.SLDPRT
cad_design/Final_Assembly/New_mount_R_2.SLDPRT
cad_design/Final_Assembly/SpurGear (1).SLDPRT
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

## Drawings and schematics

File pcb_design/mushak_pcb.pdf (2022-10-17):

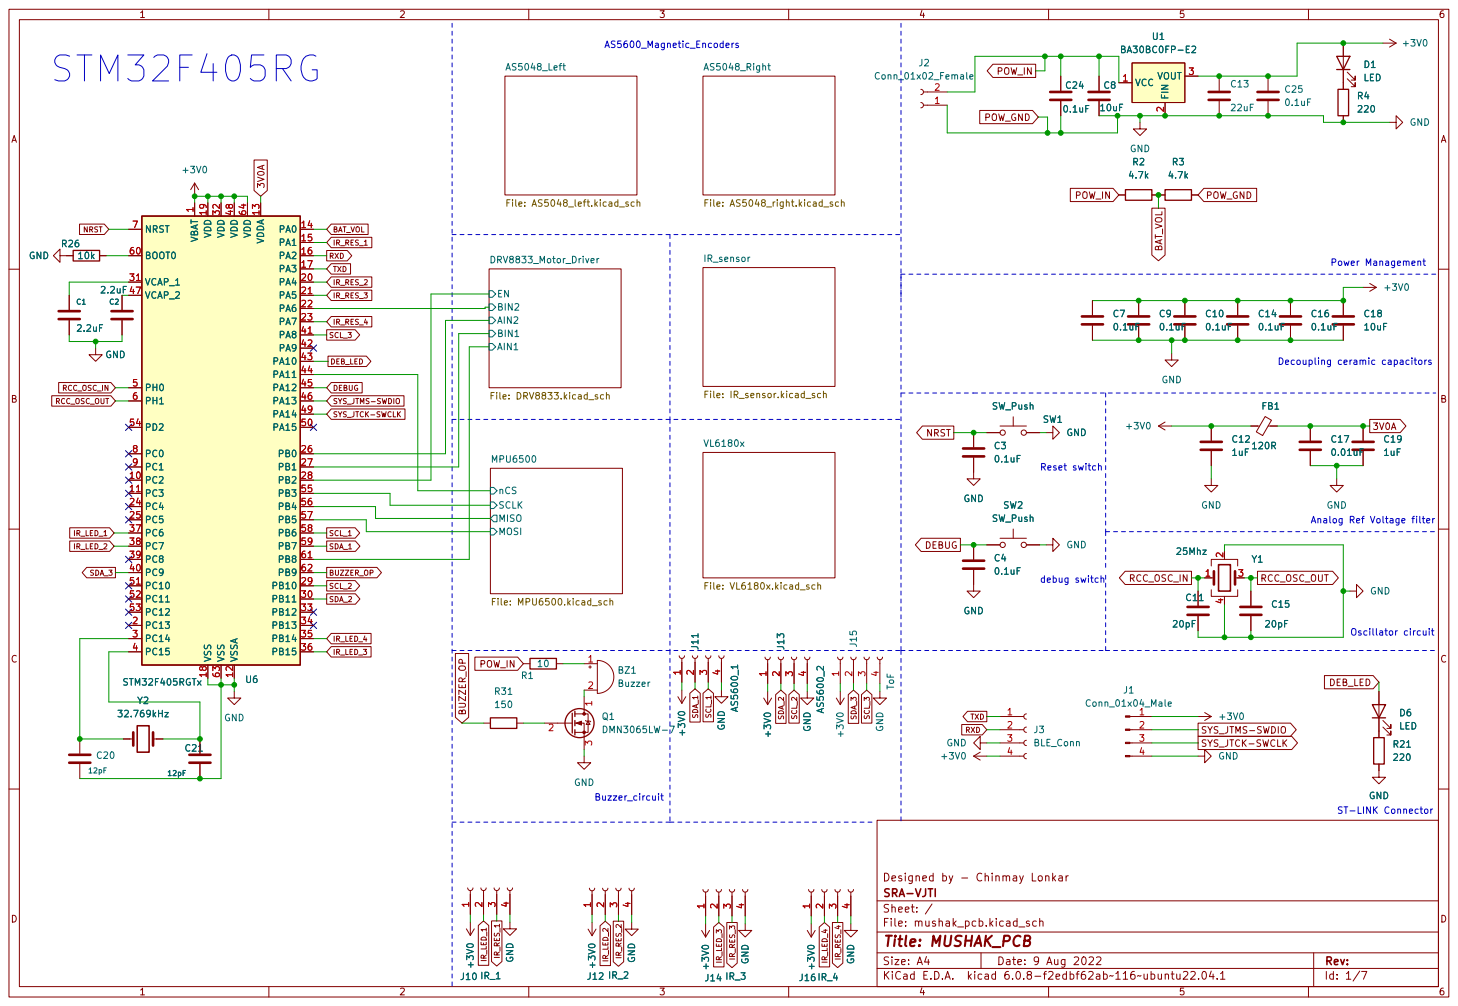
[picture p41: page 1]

Analog Ref Voltage filter R3

1 PC2 10 PC3 11 VSSA 12 VDDA 13 PA0 14 PA1 15 PA2 16 PA3 17 VSS 18 VDD 19 PC13 2 PA4 20 PA5 21 PA6 22 PA7 23 PC4 24 PC5 25 PB0 26 PB1 27 PB2 28 PB10 29 PC14 3 PB11 30 VCAP_1 31 VDD 32 PB12 33 PB13 34 PB14 35 PB15 36 PC6 37 PC7 38 PC8 39 PC15 4 PC9 40 PA8 41 PA9 42 PA10 43 PA11 44 PA12 45 PA13 46 VCAP_2 47 VDD 48 PA14 49 PH0 5 PA15 50 PC10 51 PC11 52 PC12 53 PD2 54 PB3 55 PB4 56 PB5 57 PB6 58 PB7 59 PH1 6 BOOT0 60 PB8 61 PB9 62 VSS 63 VDD 64 NRST 7 PC0 8 PC1 9 STM32F405RGTx U6 GND

1 PC2 10 PC3 11 VSSA 12 VDDA 13 PA0 14 PA1 15 PA2 16 PA3 17 VSS 18 VDD 19 PC13 2 PA4 20 PA5 21 PA6 22 PA7 23 PC4 24 PC5 25 PB0 26 PB1 27 PB2 28 PB10 29 PC14 3 PB11 30 VCAP_1 31 VDD 32 PB12 33 PB13 34 PB14 35 PB15 36 PC6 37 PC7 38 PC8 39 PC15 4 PC9 40 PA8 41 PA9 42 PA10 43 PA11 44 PA12 45 PA13 46 VCAP_2 47 VDD 48 PA14 49 PH0 5 PA15 50 PC10 51 PC11 52 PC12 53 PD2 54 PB3 55 PB4 56 PB5 57 PB6 58 PB7 59 PH1 6 BOOT0 60 PB8 61 PB9 62 VSS 63 VDD 64 NRST 7 PC0 8 PC1 9 J13 AS5600_21

File: mushak_pcb.kicad_sch Sheet: / SRA-VJTI Designed by - Chinmay Lonkar

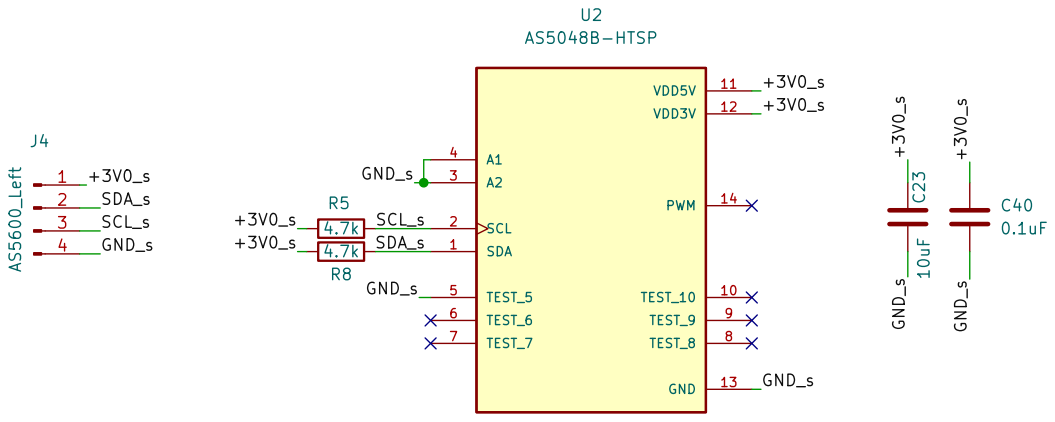
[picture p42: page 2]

Sheet: /AS5048_Left/ SRA-VJTI Designed by - Chinmay Lonkar R8

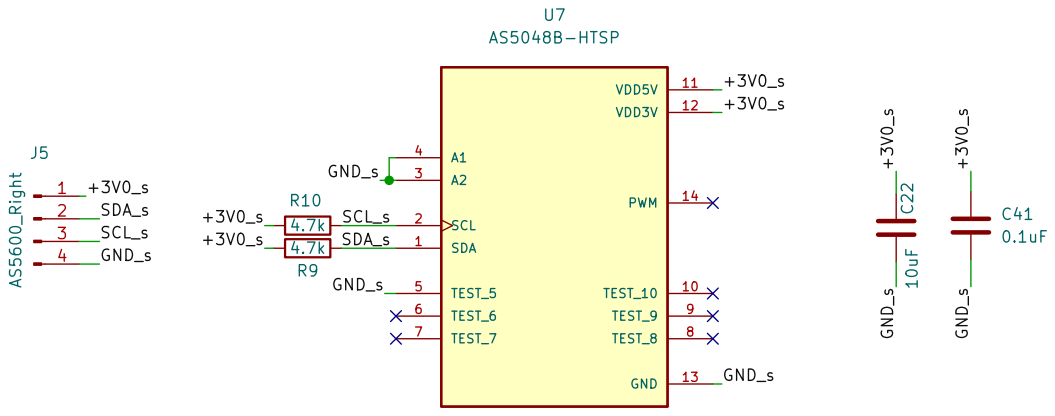
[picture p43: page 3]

Sheet: /AS5048_Right/ SRA-VJTI Designed by - Chinmay Lonkar

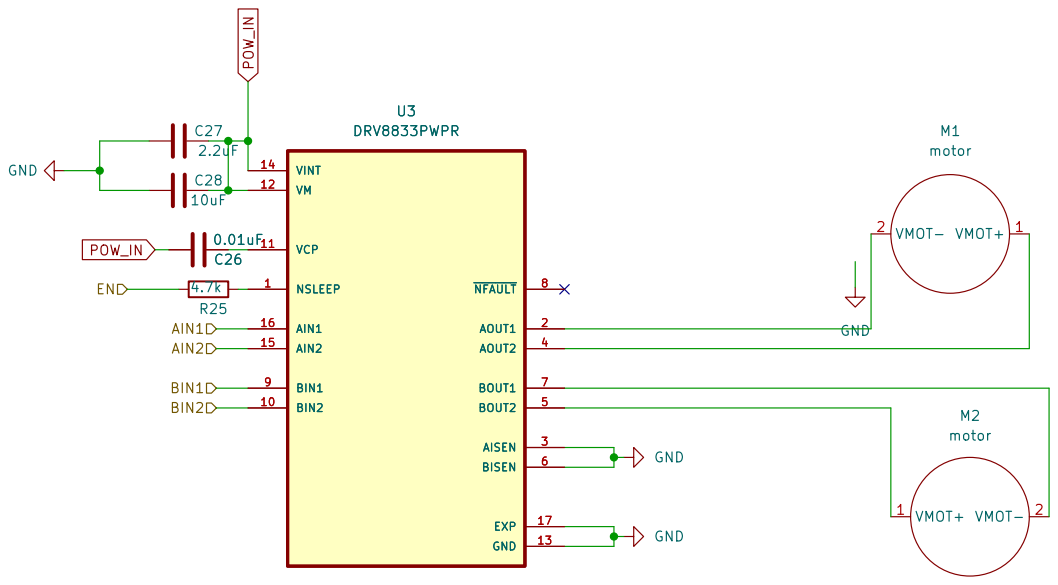
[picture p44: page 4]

Sheet: /DRV8833_Motor_Driver/ SRA-VJTI Designed by - Chinmay Lonkar GND

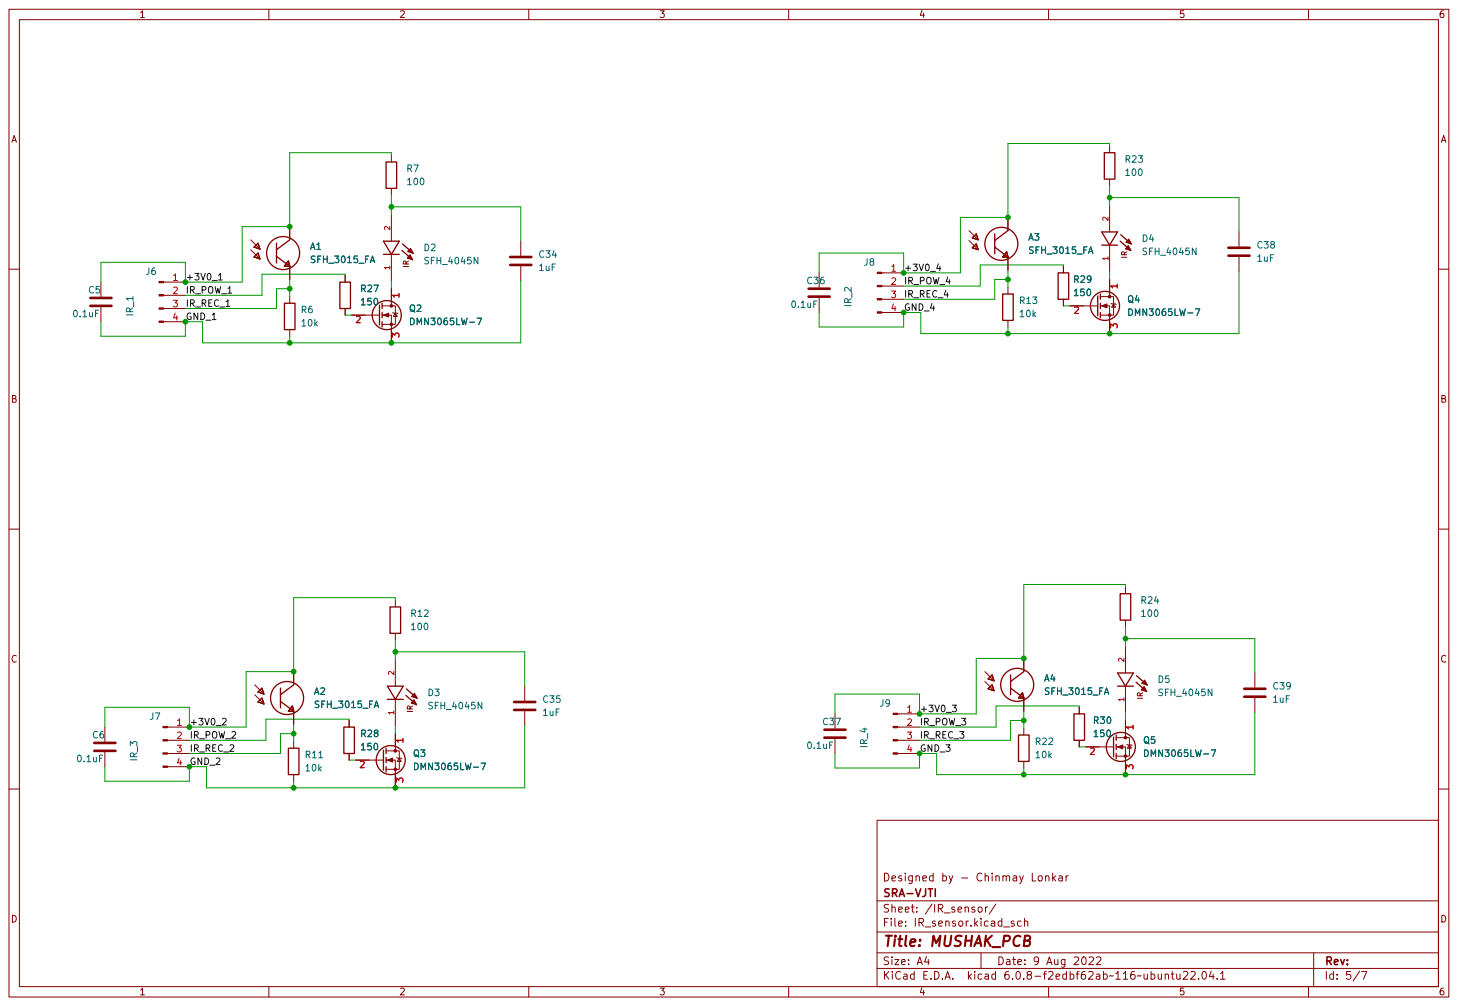
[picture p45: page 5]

Sheet: /IR_sensor/ SRA-VJTI Designed by - Chinmay Lonkar

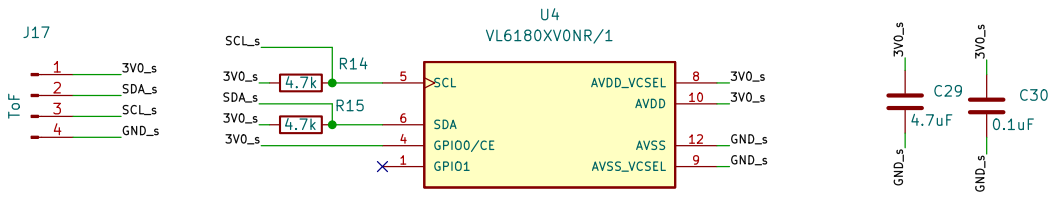
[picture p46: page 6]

File: VL6180x.kicad_sch Sheet: /VL6180x/ SRA-VJTI Designed by - Chinmay Lonkar C30

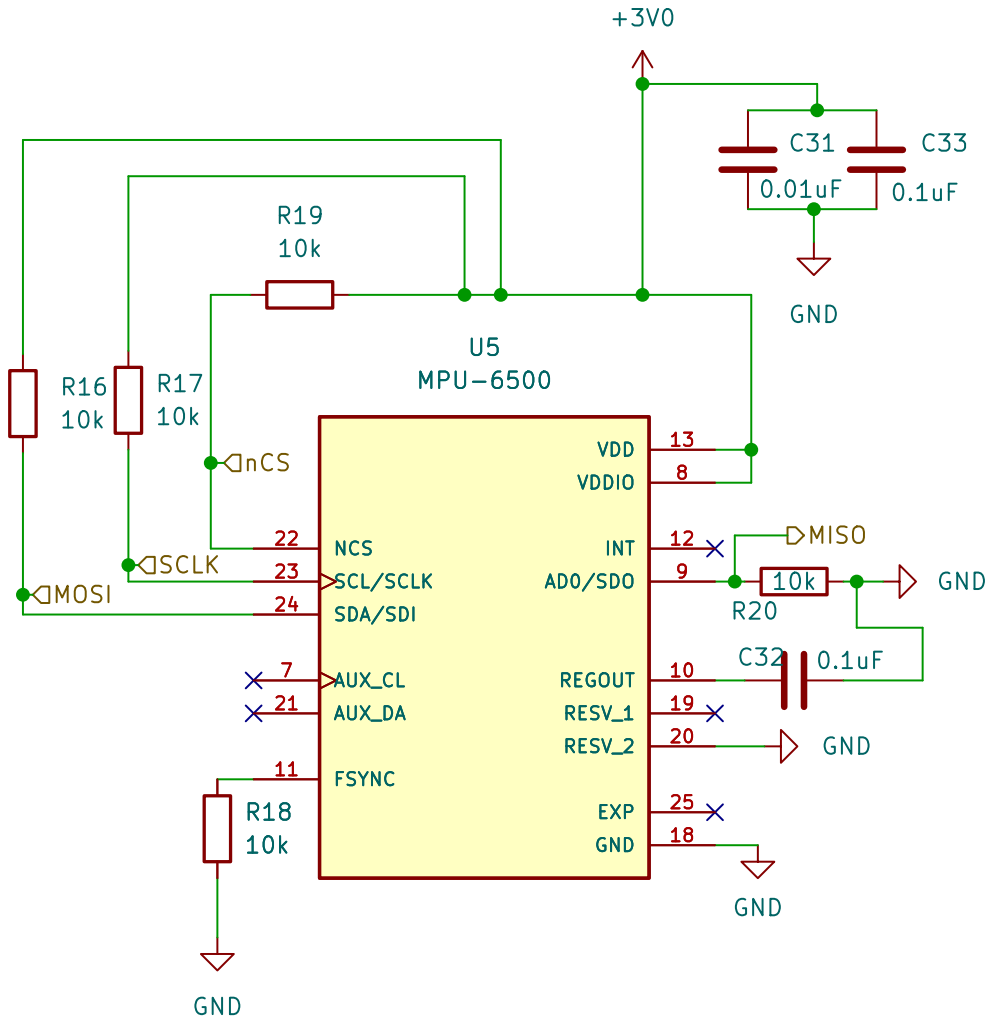
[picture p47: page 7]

File: MPU6500.kicad_sch Sheet: /MPU6500/ SRA-VJTI Designed by - Chinmay Lonkar

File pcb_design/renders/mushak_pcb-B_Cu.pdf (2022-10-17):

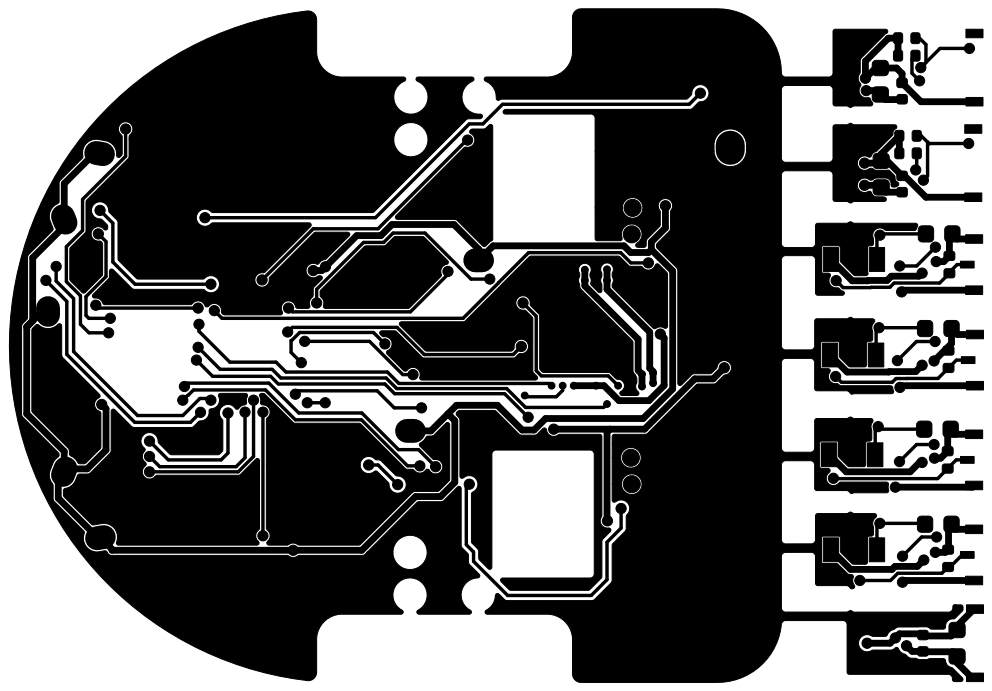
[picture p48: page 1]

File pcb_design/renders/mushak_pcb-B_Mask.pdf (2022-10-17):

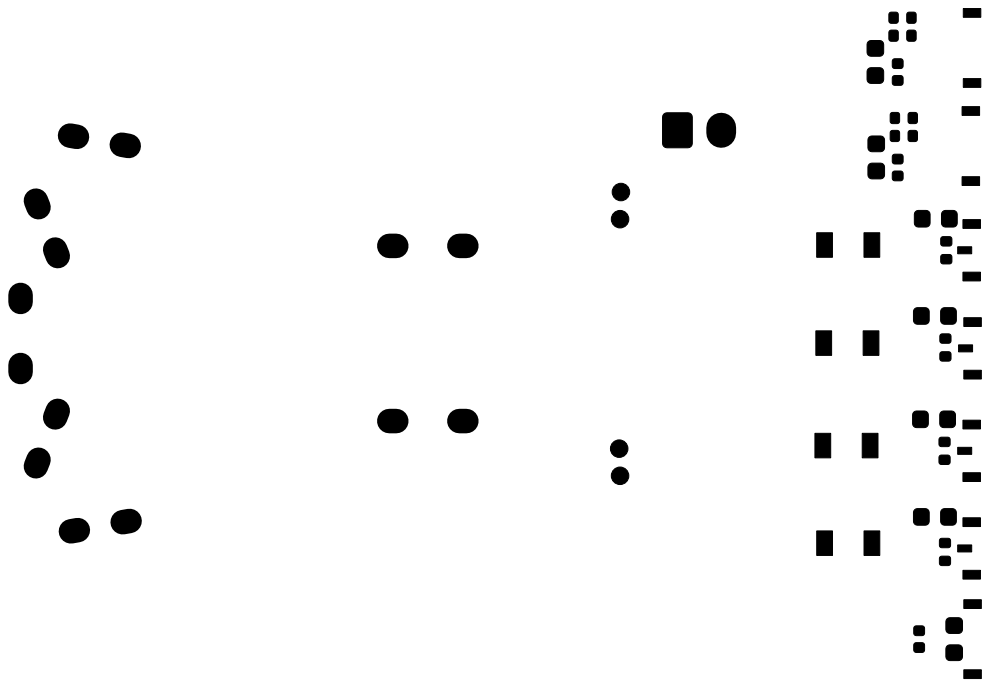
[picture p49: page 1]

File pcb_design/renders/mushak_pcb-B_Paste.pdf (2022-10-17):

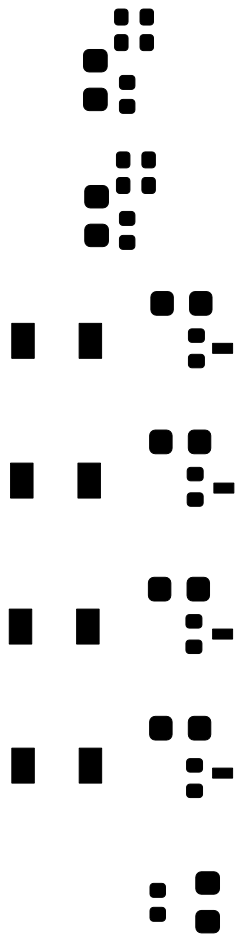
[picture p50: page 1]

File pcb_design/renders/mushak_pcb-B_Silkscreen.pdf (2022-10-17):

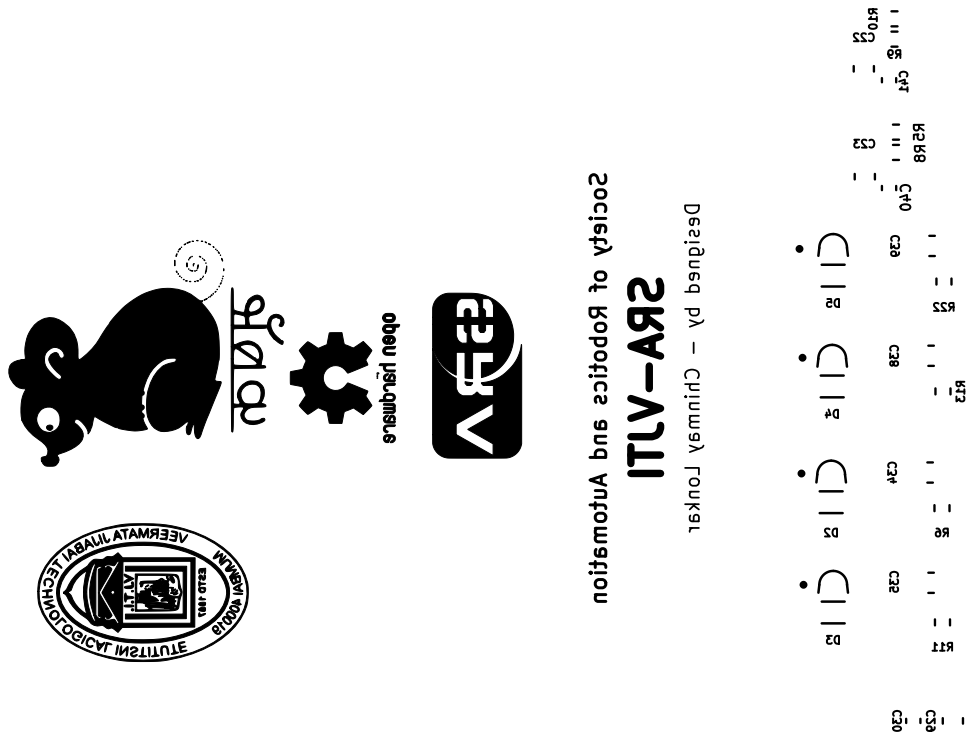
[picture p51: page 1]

Society of Robotics and Automation Designed by - Chinmay Lonkar SRA-VJTI G*** R6 R10 C41 D4 C29 C40 C38 D2 R9 R5 G***

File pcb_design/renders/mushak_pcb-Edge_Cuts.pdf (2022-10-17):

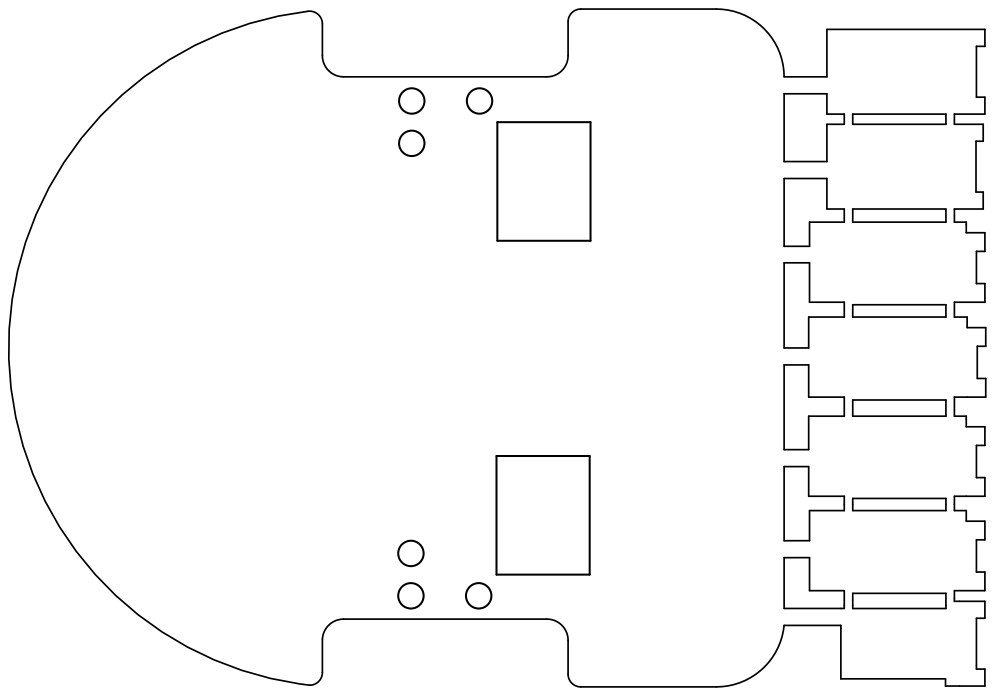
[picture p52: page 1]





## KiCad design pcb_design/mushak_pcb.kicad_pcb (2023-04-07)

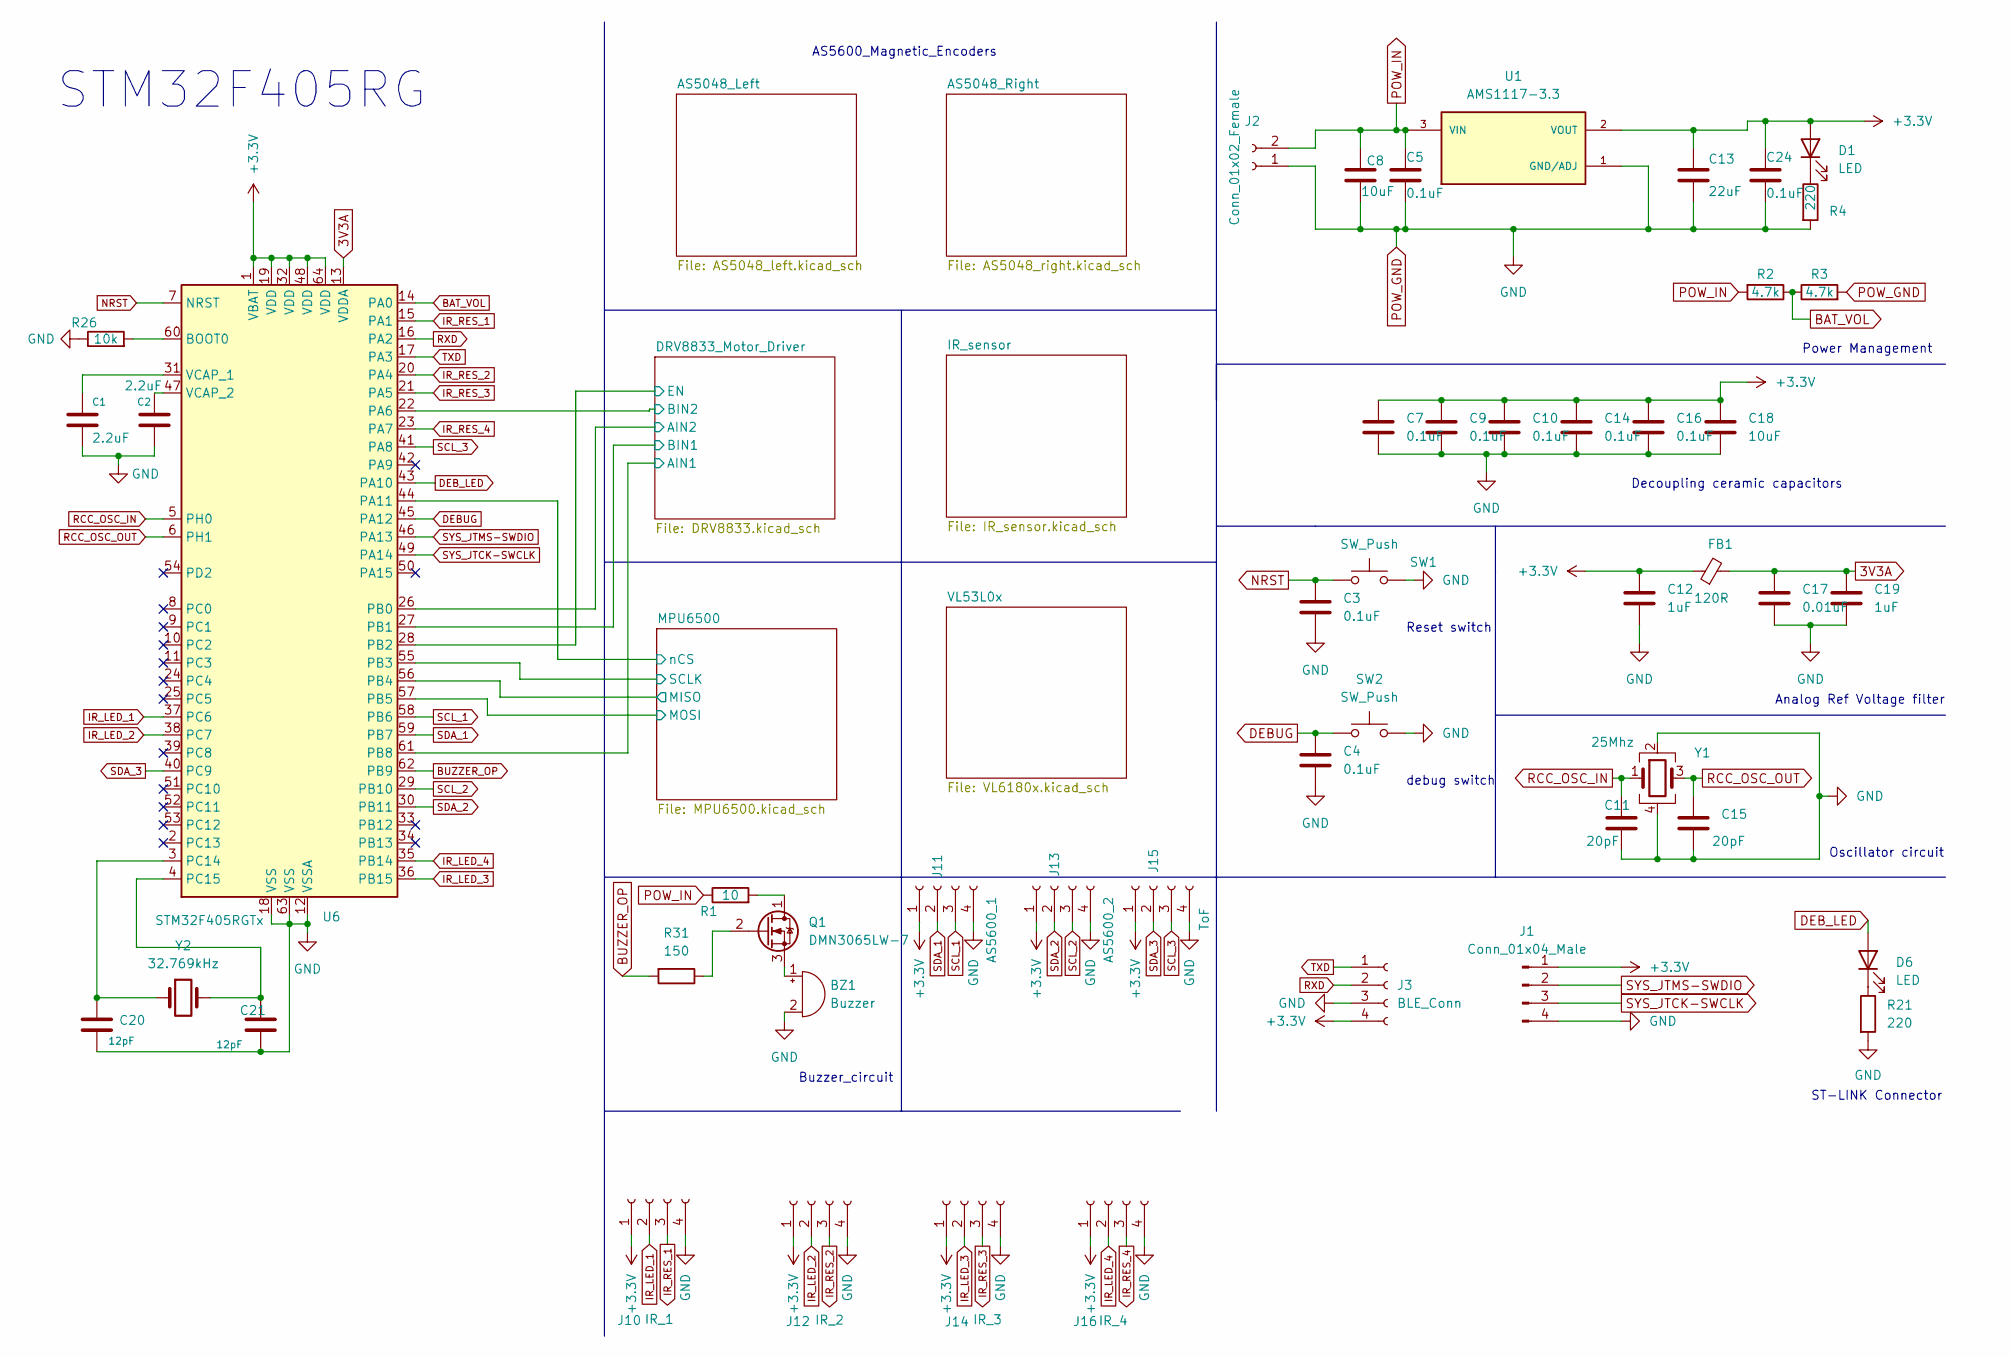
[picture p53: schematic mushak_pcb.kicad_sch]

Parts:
BZ1: Buzzer; XDCR_SMT-0440-T-R
C1, C2: 2.2uF; C_0603_1608Metric
C3, C4, C5, C7, C9, C10, C14, C16, C24: 0.1uF; C_0402_1005Metric
C8, C18: 10uF; C_0603_1608Metric
C11, C15: 20pF; C_0402_1005Metric
C12, C19: 1uF; C_0603_1608Metric
C13: 22uF; C_0603_1608Metric
C17: 0.01uF; C_0402_1005Metric
C20, C21: 12pF; C_0402_1005Metric
D1, D6: LED; LED_0402_1005Metric
FB1: 120R; L_0805_2012Metric
J1: Conn_01x04_Male; JST_SH_BM04B-SRSS-TB_1x04-1MP_P1.00mm_Vertical
J2: Conn_01x02_Female; JST_EH_B2B-EH-A_1x02_P2.50mm_Vertical
J3: BLE_Conn; JST_SH_BM04B-SRSS-TB_1x04-1MP_P1.00mm_Vertical
J10: IR_1; IR_HOST_V_04
J11: AS5600_1; STAND_HOST_04
J12: IR_2; IR_HOST_V_04
J13: AS5600_2; STAND_HOST_04
J14: IR_3; IR_HOST_V_04
J15: ToF; STAND_HOST_04
J16: IR_4; IR_HOST_V_04
Q1: DMN3065LW-7; SOT-323_SC-70
R1: 10; R_0603_1608Metric
R2, R3: 4.7k; R_0402_1005Metric
R4, R21: 220; R_0603_1608Metric
R26: 10k; R_0402_1005Metric
R31: 150; R_0402_1005Metric
SW1, SW2: SW_Push; SW_TL1015AF160QG
U1: AMS1117-3.3; SOT229P700X180-4N; PARTREV N/A
U6: STM32F405RGTx; LQFP-64_10x10mm_P0.5mm
Y1: 25Mhz; Crystal_SMD_3225-4Pin_3.2x2.5mm
Y2: 32.769kHz; XTAL_ABS07-32.768KHZ-T

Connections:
3V3A: C17.1, C19.1, FB1.2, U6.13 (VDDA)
+3.3V: C7.1, C9.1, C10.1, C12.1, C13.1, C14.1, C16.1, C18.1, C24.1, D1.2 (A), FB1.1, J1.1, J3.4, J10.1, J11.1, J12.1, J13.1, J14.1, J15.1, J16.1, U1.2 (VOUT), U6.1 (VBAT), U6.19 (VDD), U6.32 (VDD), U6.48 (VDD), U6.64 (VDD); also elsewhere on the board
/DRV8833_Motor_Driver/AIN1: U6.61 (PB8); also elsewhere on the board
/DRV8833_Motor_Driver/AIN2: U6.26 (PB0); also elsewhere on the board
/DRV8833_Motor_Driver/BIN1: U6.27 (PB1); also elsewhere on the board
/DRV8833_Motor_Driver/BIN2: U6.22 (PA6); also elsewhere on the board
/DRV8833_Motor_Driver/EN: U6.28 (PB2); also elsewhere on the board
/MPU6500/MISO: U6.56 (PB4); also elsewhere on the board
/MPU6500/MOSI: U6.57 (PB5); also elsewhere on the board
/MPU6500/SCLK: U6.55 (PB3); also elsewhere on the board
/MPU6500/nCS: U6.44 (PA11); also elsewhere on the board
BAT_VOL: R2.1, R3.1, U6.14 (PA0)
BUZZER_OP: R31.2, U6.62 (PB9)
DEBUG: C4.1, SW2.1, U6.45 (PA12)
DEB_LED: D6.2 (A), U6.43 (PA10)
IR_LED_1: J10.2, U6.37 (PC6)
IR_LED_2: J12.2, U6.38 (PC7)
IR_LED_3: J14.2, U6.36 (PB15)
IR_LED_4: J16.2, U6.35 (PB14)
IR_RES_1: J10.3, U6.15 (PA1)
IR_RES_2: J12.3, U6.20 (PA4)
IR_RES_3: J14.3, U6.21 (PA5)
IR_RES_4: J16.3, U6.23 (PA7)
NRST: C3.1, SW1.1, U6.7 (NRST)
unnamed: BZ1.1 (-), Q1.3 (S)
unnamed: C1.1, U6.31 (VCAP_1)
unnamed: C2.1, U6.47 (VCAP_2)
unnamed: C20.1, U6.3 (PC14), Y2.1
unnamed: C21.1, U6.4 (PC15), Y2.2
unnamed: D1.1 (K), R4.1
unnamed: D6.1 (K), R21.1
unnamed: Q1.1 (D), R1.2
unnamed: Q1.2 (G), R31.1
unnamed: R26.2, U6.60 (BOOT0)
POW_GND: BZ1.2 (+), C1.2, C2.2, C3.2, C4.2, C5.2, C7.2, C8.2, C9.2, C10.2, C11.2, C12.2, C13.2, C14.2, C15.2, C16.2, C17.2, C18.2, C19.2, C20.2, C21.2, C24.2, J1.4, J2.1, J3.3, J10.4, J11.4, J12.4, J13.4, J14.4, J15.4, J16.4, R3.2, R4.2, R21.2, R26.1, SW1.2, SW2.2, U1.1 (GND/ADJ), U6.12 (VSSA), U6.18 (VSS), U6.63 (VSS), Y1.2, Y1.4; also elsewhere on the board
POW_IN: C5.1, C8.1, J2.2, R1.1, R2.2, U1.3 (VIN); also elsewhere on the board
RCC_OSC_IN: C11.1, U6.5 (PH0), Y1.1
RCC_OSC_OUT: C15.1, U6.6 (PH1), Y1.3
RXD: J3.2, U6.16 (PA2)
SCL_1: J11.3, U6.58 (PB6)
SCL_2: J13.3, U6.29 (PB10)
SCL_3: J15.3, U6.41 (PA8)
SDA_1: J11.2, U6.59 (PB7)
SDA_2: J13.2, U6.30 (PB11)
SDA_3: J15.2, U6.40 (PC9)
SYS_JTCK-SWCLK: J1.3, U6.49 (PA14)
SYS_JTMS-SWDIO: J1.2, U6.46 (PA13)
TXD: J3.1, U6.17 (PA3)

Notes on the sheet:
Power Management
debug switch
Decoupling ceramic capacitors
ST-LINK Connector
Analog Ref Voltage filter
Buzzer_circuit
Reset switch
AS5600_Magnetic_Encoders
STM32F405RG
Oscillator circuit

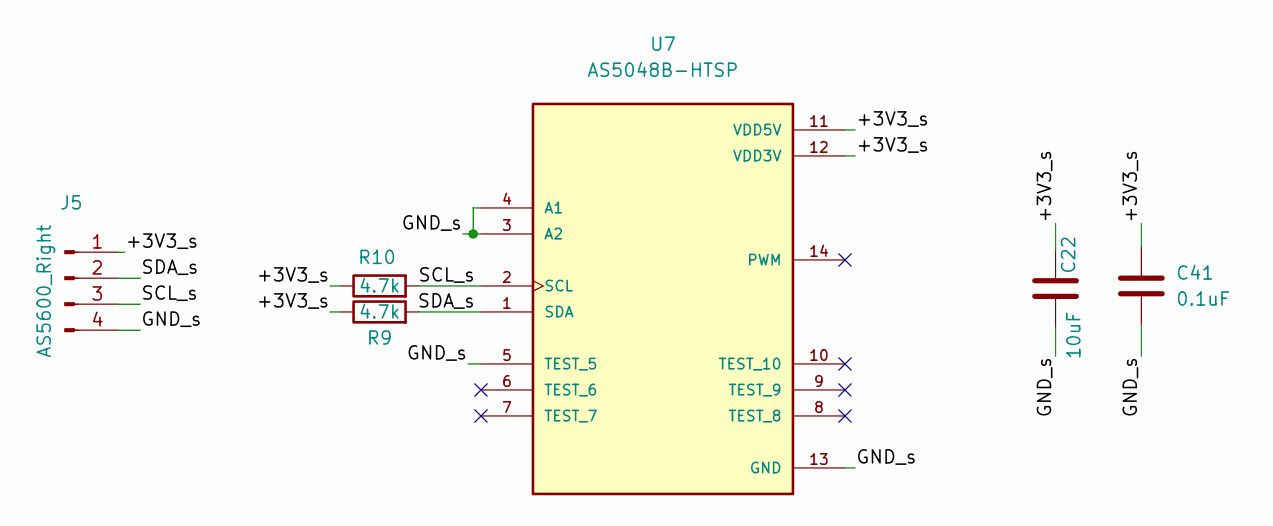
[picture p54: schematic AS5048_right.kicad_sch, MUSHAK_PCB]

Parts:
C22: 10uF; C_0603_1608Metric
C41: 0.1uF; C_0402_1005Metric
J5: AS5600_Right; STAND_SLAVE_04
R9, R10: 4.7k; R_0402_1005Metric
U7: AS5048B-HTSP; SOP65P640X120-14N; PARTREV 1-11

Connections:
/AS5048_Right/+3V3_s: C22.2, C41.1, J5.1, R9.1, R10.1, U7.11 (VDD5V), U7.12 (VDD3V)
/AS5048_Right/GND_s: C22.1, C41.2, J5.4, U7.3 (A2), U7.4 (A1), U7.5 (TEST_5), U7.13 (GND)
/AS5048_Right/SCL_s: J5.3, R10.2, U7.2 (SCL)
/AS5048_Right/SDA_s: J5.2, R9.2, U7.1 (SDA)

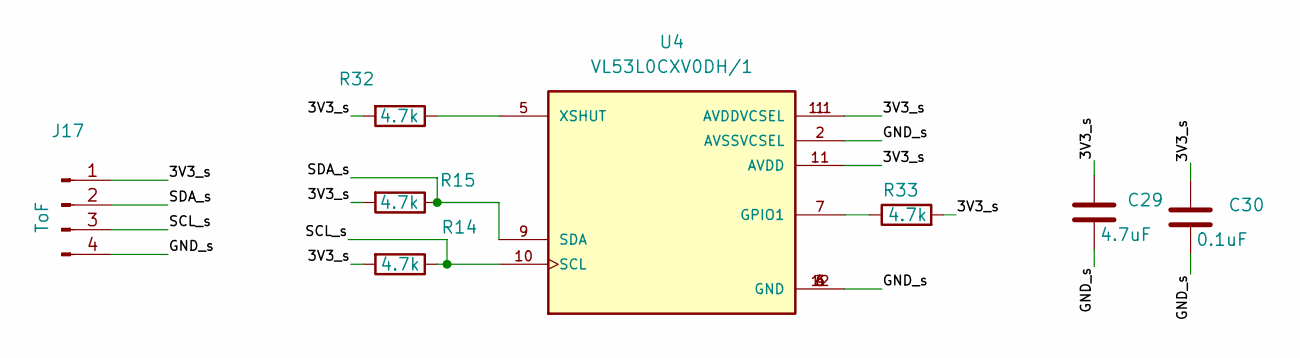
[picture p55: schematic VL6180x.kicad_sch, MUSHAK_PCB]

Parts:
C29: 4.7uF; C_0603_1608Metric
C30: 0.1uF; C_0402_1005Metric
J17: ToF; STAND_SLAVE_04
R14, R15, R32, R33: 4.7k; R_0402_1005Metric
U4: VL53L0CXV0DH/1; XDCR_VL53L0CXV0DH_1

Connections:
/VL53L0x/3V3_s: C29.1, C30.1, J17.1, R14.2, R15.2, R32.2, R33.2, U4.1 (AVDDVCSEL), U4.1.1 (AVDDVCSEL), U4.11 (AVDD)
/VL53L0x/GND_s: C29.2, C30.2, J17.4, U4.2 (AVSSVCSEL), U4.3 (GND), U4.4 (GND), U4.6 (GND), U4.12 (GND)
/VL53L0x/SCL_s: J17.3, R14.1, U4.10 (SCL)
/VL53L0x/SDA_s: J17.2, R15.1, U4.9 (SDA)
unnamed: R32.1, U4.5 (XSHUT)
unnamed: R33.1, U4.7 (GPIO1)

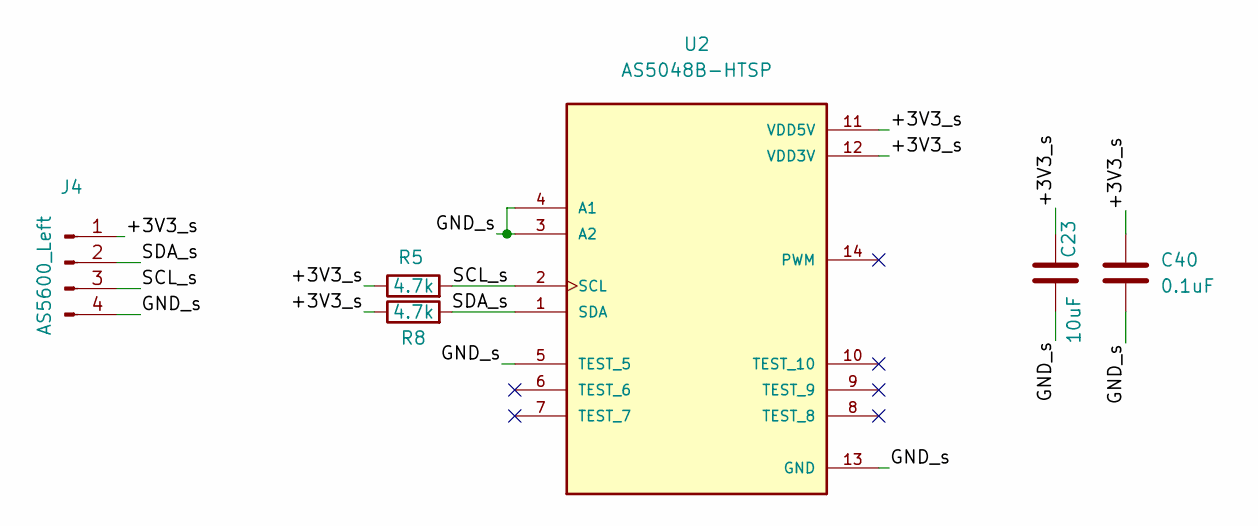
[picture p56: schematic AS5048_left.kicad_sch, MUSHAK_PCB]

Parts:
C23: 10uF; C_0603_1608Metric
C40: 0.1uF; C_0402_1005Metric
J4: AS5600_Left; STAND_SLAVE_04
R5, R8: 4.7k; R_0402_1005Metric
U2: AS5048B-HTSP; SOP65P640X120-14N; PARTREV 1-11

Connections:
/AS5048_Left/+3V3_s: C23.2, C40.1, J4.1, R5.1, R8.1, U2.11 (VDD5V), U2.12 (VDD3V)
/AS5048_Left/GND_s: C23.1, C40.2, J4.4, U2.3 (A2), U2.4 (A1), U2.5 (TEST_5), U2.13 (GND)
/AS5048_Left/SCL_s: J4.3, R5.2, U2.2 (SCL)
/AS5048_Left/SDA_s: J4.2, R8.2, U2.1 (SDA)

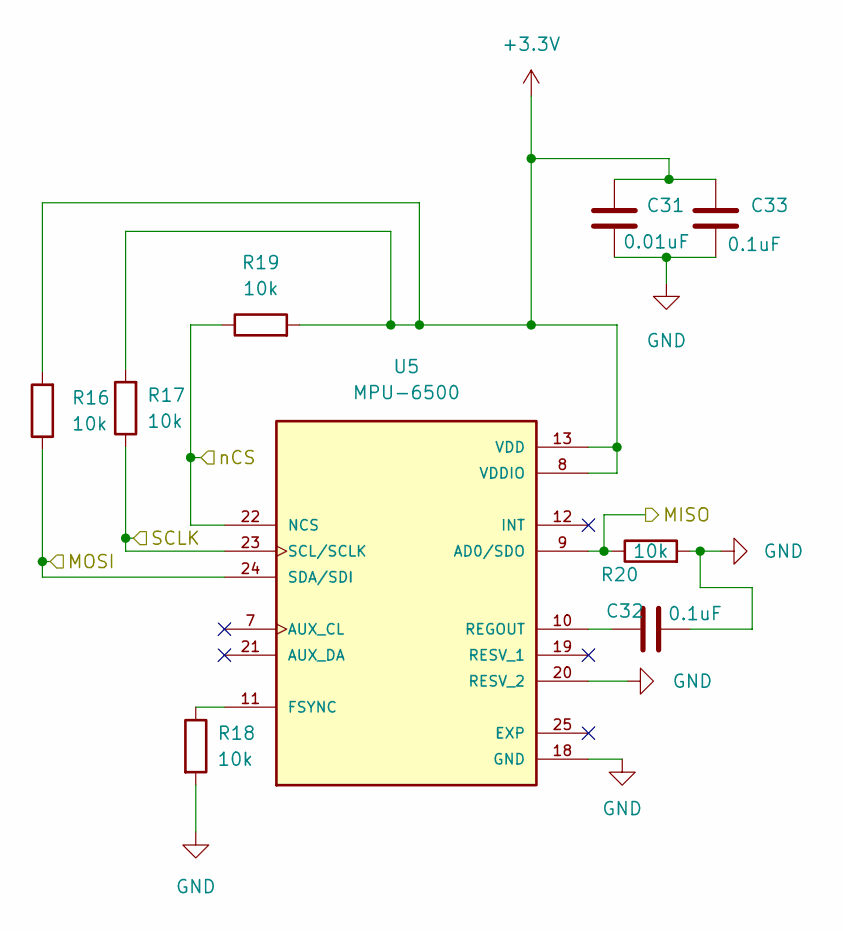
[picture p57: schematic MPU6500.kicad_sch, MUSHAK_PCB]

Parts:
C31: 0.01uF; C_0402_1005Metric
C32, C33: 0.1uF; C_0402_1005Metric
R16, R17, R18, R19, R20: 10k; R_0402_1005Metric
U5: MPU-6500; QFN40P300X300X95-25N; PARTREV 1.3

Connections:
+3.3V: C31.1, C33.1, R16.2, R17.2, R19.2, U5.8 (VDDIO), U5.13 (VDD); also elsewhere on the board
/MPU6500/MISO: R20.1, U5.9 (AD0/SDO); also elsewhere on the board
/MPU6500/MOSI: R16.1, U5.24 (SDA/SDI); also elsewhere on the board
/MPU6500/SCLK: R17.1, U5.23 (SCL/SCLK); also elsewhere on the board
/MPU6500/nCS: R19.1, U5.22 (NCS); also elsewhere on the board
unnamed: C32.2, U5.10 (REGOUT)
unnamed: R18.1, U5.11 (FSYNC)
POW_GND: C31.2, C32.1, C33.2, R18.2, R20.2, U5.18 (GND), U5.20 (RESV_2); also elsewhere on the board

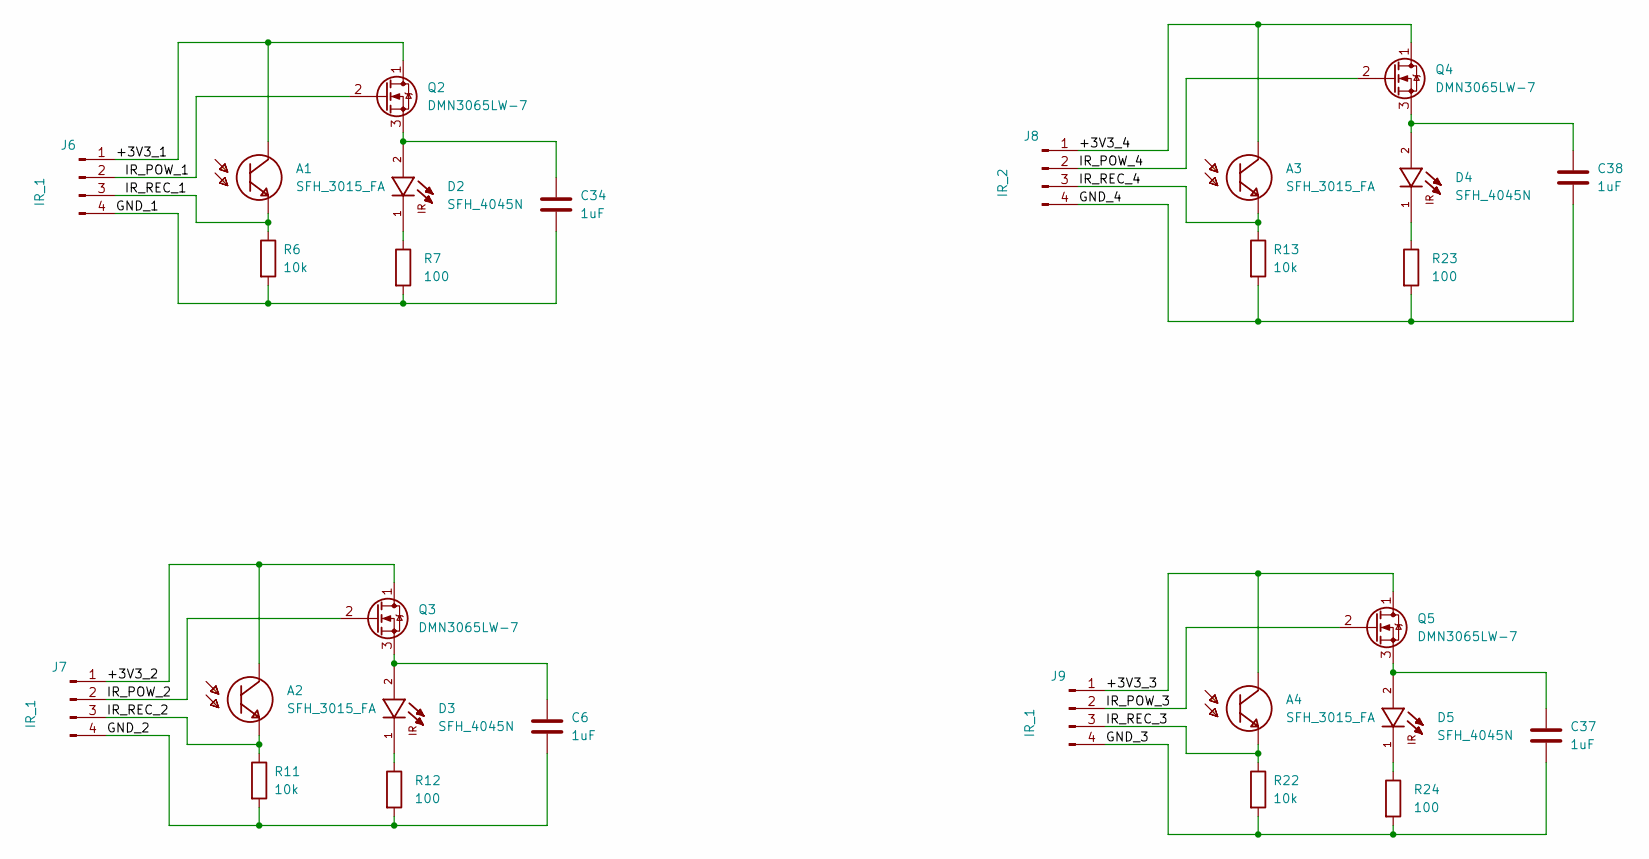
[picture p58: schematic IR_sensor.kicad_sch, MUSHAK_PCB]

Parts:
A1, A2, A3, A4: SFH_3015_FA; XDCR_SFH_3015_FA; PARTREV 1.6
C6, C34, C37, C38: 1uF; C_0603_1608Metric
D2, D3, D4, D5: SFH_4045N; LED_SFH_4045N; PARTREV 1.5
J6, J7, J9: IR_1; IR_SLAVE_V_04
J8: IR_2; IR_SLAVE_V_04
Q2, Q3, Q4, Q5: DMN3065LW-7; SOT-323_SC-70
R6, R11, R13, R22: 10k; R_0402_1005Metric
R7, R12, R23, R24: 100; R_0603_1608Metric

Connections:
/IR_sensor/+3V3_1: A1.2, J6.1, Q2.1 (D)
/IR_sensor/+3V3_2: A2.2, J7.1, Q3.1 (D)
/IR_sensor/+3V3_3: A4.2, J9.1, Q5.1 (D)
/IR_sensor/+3V3_4: A3.2, J8.1, Q4.1 (D)
/IR_sensor/GND_1: C34.2, J6.4, R6.2, R7.2
/IR_sensor/GND_2: C6.2, J7.4, R11.2, R12.2
/IR_sensor/GND_3: C37.2, J9.4, R22.2, R24.2
/IR_sensor/GND_4: C38.2, J8.4, R13.2, R23.2
/IR_sensor/IR_POW_1: J6.2, Q2.2 (G)
/IR_sensor/IR_POW_2: J7.2, Q3.2 (G)
/IR_sensor/IR_POW_3: J9.2, Q5.2 (G)
/IR_sensor/IR_POW_4: J8.2, Q4.2 (G)
/IR_sensor/IR_REC_1: A1.1, J6.3, R6.1
/IR_sensor/IR_REC_2: A2.1, J7.3, R11.1
/IR_sensor/IR_REC_3: A4.1, J9.3, R22.1
/IR_sensor/IR_REC_4: A3.1, J8.3, R13.1
unnamed: C6.1, D3.2, Q3.3 (S)
unnamed: C34.1, D2.2, Q2.3 (S)
unnamed: C37.1, D5.2, Q5.3 (S)
unnamed: C38.1, D4.2, Q4.3 (S)
unnamed: D2.1, R7.1
unnamed: D3.1, R12.1
unnamed: D4.1, R23.1
unnamed: D5.1, R24.1

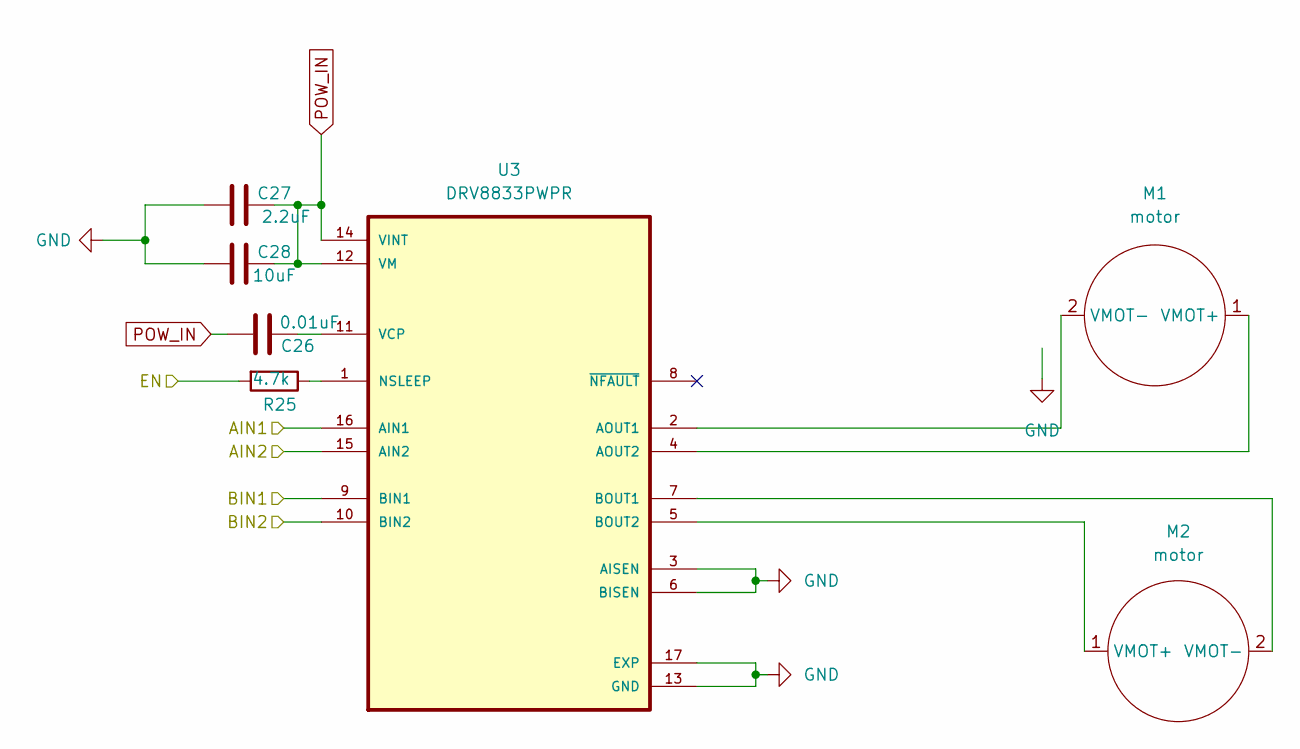
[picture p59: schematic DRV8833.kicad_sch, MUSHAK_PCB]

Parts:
C26: 0.01uF; C_0402_1005Metric
C27: 2.2uF; C_0603_1608Metric
C28: 10uF; C_0603_1608Metric
M1, M2: motor
R25: 4.7k; R_0402_1005Metric
U3: DRV8833PWPR; IC_DRV8833PWPR; PARTREV E

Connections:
/DRV8833_Motor_Driver/AIN1: U3.16 (AIN1); also elsewhere on the board
/DRV8833_Motor_Driver/AIN2: U3.15 (AIN2); also elsewhere on the board
/DRV8833_Motor_Driver/BIN1: U3.9 (BIN1); also elsewhere on the board
/DRV8833_Motor_Driver/BIN2: U3.10 (BIN2); also elsewhere on the board
/DRV8833_Motor_Driver/EN: R25.2; also elsewhere on the board
unnamed: C26.2, U3.11 (VCP)
unnamed: M1.1 (VMOT+), U3.4 (AOUT2)
unnamed: M1.2 (VMOT-), U3.2 (AOUT1)
unnamed: M2.1 (VMOT+), U3.5 (BOUT2)
unnamed: M2.2 (VMOT-), U3.7 (BOUT1)
unnamed: R25.1, U3.1 (NSLEEP)
POW_GND: C27.1, C28.1, U3.3 (AISEN), U3.6 (BISEN), U3.13 (GND), U3.17 (EXP); also elsewhere on the board
POW_IN: C26.1, C27.2, C28.2, U3.12 (VM), U3.14 (VINT); also elsewhere on the board

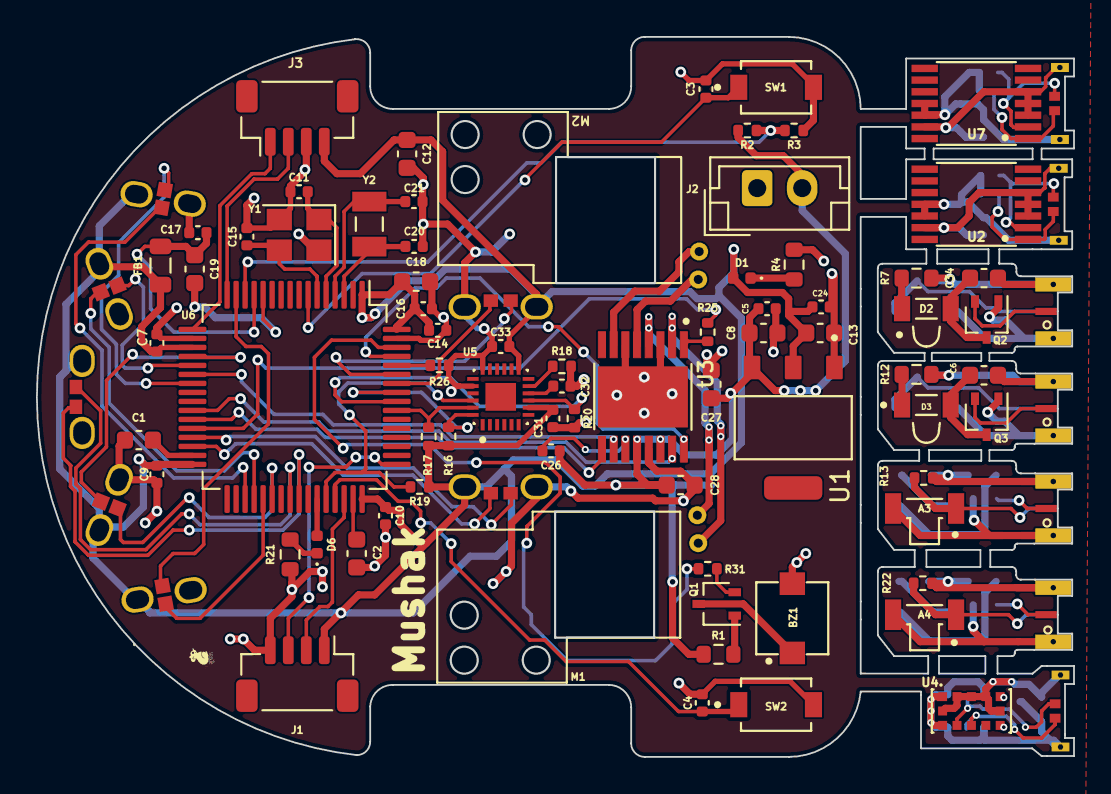
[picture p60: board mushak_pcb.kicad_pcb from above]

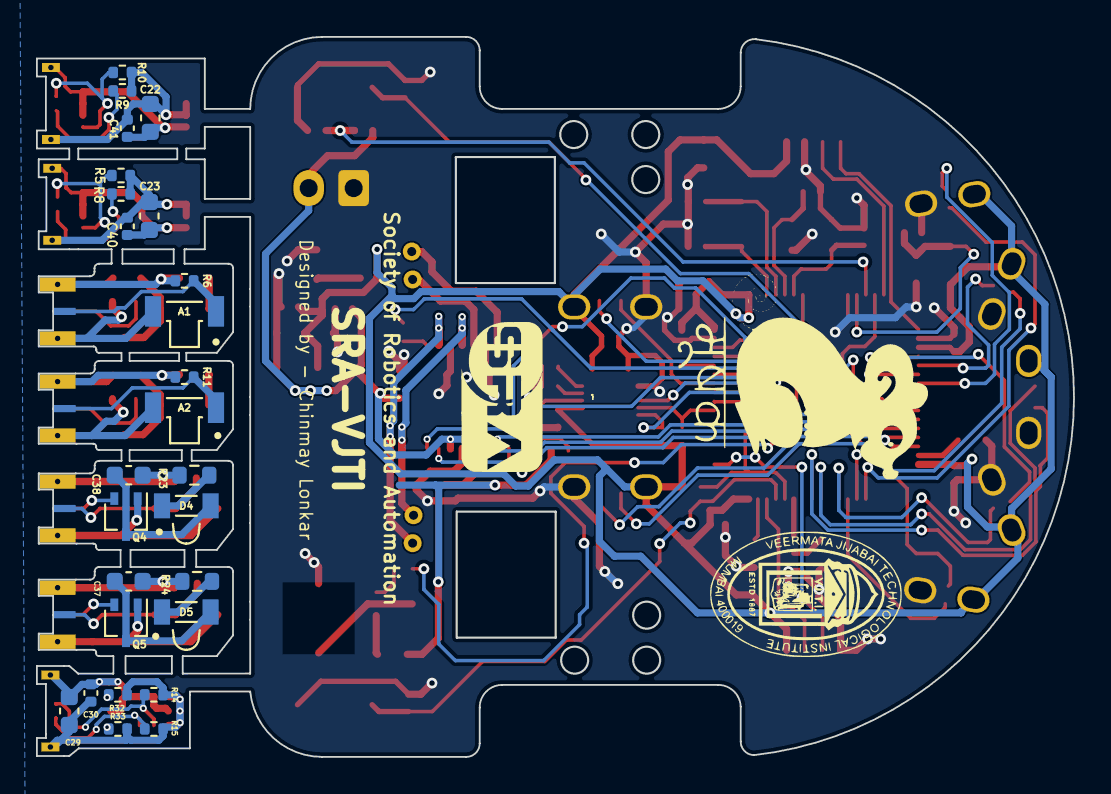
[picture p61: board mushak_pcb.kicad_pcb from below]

Board: 2 copper layers, 57.6 x 40.0 mm, 113 parts (27 on the bottom side), 94 nets.

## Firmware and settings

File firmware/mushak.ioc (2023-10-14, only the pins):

Mcu.UserName=STM32F405RGTx
PA0-WKUP.Signal=ADCx_IN0
PA1.Signal=ADCx_IN1
PA10.GPIO_Label=DEBUG_LED
PA10.Signal=GPIO_Output
PA11.GPIO_Label=MPU6500_CS
PA11.Signal=GPIO_Output
PA12.GPIO_Label=DEBUG_BTN
PA12.Signal=GPIO_Input
PA13.Signal=SYS_JTMS-SWDIO
PA14.Signal=SYS_JTCK-SWCLK
PA2.Signal=USART2_TX
PA3.Signal=USART2_RX
PA4.Signal=ADCx_IN4
PA5.Signal=ADCx_IN5
PA6.Signal=S_TIM13_CH1
PA7.Signal=ADCx_IN7
PA8.Signal=I2C3_SCL
PB0.Signal=S_TIM3_CH3
PB1.Signal=S_TIM3_CH4
PB10.Signal=I2C2_SCL
PB11.Signal=I2C2_SDA
PB14.Signal=S_TIM12_CH1
PB15.Signal=S_TIM12_CH2
PB2.GPIO_Label=DRV8833_EN
PB2.Signal=GPIO_Output
PB3.Signal=SPI1_SCK
PB4.Signal=SPI1_MISO
PB5.Signal=SPI1_MOSI
PB6.Signal=I2C1_SCL
PB7.Signal=I2C1_SDA
PB8.Signal=S_TIM10_CH1
PB9.Signal=S_TIM11_CH1
PC14-OSC32_IN.Signal=RCC_OSC32_IN
PC15-OSC32_OUT.Signal=RCC_OSC32_OUT
PC6.Signal=S_TIM3_CH1
PC7.Signal=S_TIM3_CH2
PC9.Signal=I2C3_SDA
PH0-OSC_IN.Signal=RCC_OSC_IN
PH1-OSC_OUT.Signal=RCC_OSC_OUT

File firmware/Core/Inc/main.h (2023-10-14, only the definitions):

#define DEBUG_LED_Pin GPIO_PIN_10
#define DEBUG_LED_GPIO_Port GPIOA
#define MPU6500_CS_Pin GPIO_PIN_11
#define MPU6500_CS_GPIO_Port GPIOA
#define DEBUG_BTN_Pin GPIO_PIN_12
#define DEBUG_BTN_GPIO_Port GPIOA

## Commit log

2022-07-19 Add I2C library and VL6180x driver
2022-07-19 Add AS5600 driver
2022-07-20 Correct the typo of i2c in Makefile
2022-07-20 Solve I2C_Handler bug
2022-08-05 update VL6180x driver
2022-08-09 Add MPU6500 driver
2022-08-15 Add DRV8833 driver api
2022-08-28 PCB Design for Mushak (#2)
    * Add Schematic for stm32F405
    * changed footprints of capacitors and resistors
    * made draft pcb footprint placement
    * Add 3d models to footprint
    * updated footprint for motors
    * corrected encoder and motor driver schematics
    * VL6180x part routed
    * changed footprint of passive components
    * Started Poer trace routing
    * completed routing
    * Completed sensor routing
    * modified pcb outline and graphics
    * modified graphics
    * Updated graphics and added dimensions
    [ABS07-32.768KHZ-T.step, AS5600.stp, AS5600_left.kicad_sch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]
2022-08-28 Add PCB images
2022-08-29 PCB_Readme (#3)
    * Add readme and change sensor angles
    * Add README for PCB Design
    * CHanged angles for IR Sensor placement
    [ABS07-32.768KHZ-T.step, AS5600.stp, AS5600_left.kicad_sch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]
2022-08-30 Added CAD Design
    [300mAh_Lipo_Battery.step, Assem2.SLDASM, Assem24.SLDASM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]
2022-08-30 Add the CAD Design in README.md
2022-08-30 Improved File Structure
    [300mAh_Lipo_Battery.step, Assem2.SLDASM, Assem24.SLDASM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]
2022-08-30 PCB Design Readme (#4)
    Update PCB Readme.md
2022-08-30 Add gerbers
    [mushak_pcb-B_Cu.gbr, mushak_pcb-B_Mask.gbr, mushak_pcb-B_Paste.gbr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]
2022-08-30 add graphiccs on PCB
    [mushak_pcb-B_Cu.gbr, mushak_pcb-B_Mask.gbr, mushak_pcb-B_Paste.gbr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]
2022-08-30 Update the pcb notation image
2022-08-31 Add schematics pdf to pcb_design folder
2022-09-02 Add BOM to pcb_design
    [BOM.csv]
2022-09-15 changed AS5600 to AS5048B
    [AS5600_left.kicad_sch, AS5600_right.kicad_sch, DRV8833.kicad_sch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]
2022-09-15 change capacitor silkscreen placement
    [mushak_pcb.kicad_pcb]
2022-09-18 modified capacitors for encoders
    [AS5048_left.kicad_sch, AS5048_right.kicad_sch, AS5600_left.kicad_sch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]
2022-09-18 update gerbers
    [BOM.csv, Mushak_PCB_BoM.xlsx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]
2022-09-29 Add resistors between MOSFET gate
    [AS5048_left.kicad_sch, AS5048_right.kicad_sch, IR_sensor.kicad_sch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]
2022-09-30 resolved routing errors
    [mushak_pcb-B_Cu.gbr, mushak_pcb-B_Mask.gbr, mushak_pcb-B_Paste.gbr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]
2022-09-30 updated BoM
    [BOM.csv, Mushak_PCB_BoM.xlsx, mushak_pcb.kicad_pcb]
2022-10-11 Correct BoM and placement files
    [BOM.csv, BoM.xlsx, DRV8833.kicad_sch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]
2022-10-11 update schematics pdf
2022-10-12 enlarge PCB hole size
    [mushak_pcb.kicad_pcb]
2022-10-12 Update placement files
    [mushak_pcb-top-pos.csv]
2022-10-15 Update PCB as per manufacturing requirements
    [BoM.xlsx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]
2022-10-15 modify silkscreen
    [mushak_pcb-B_Cu.gbr, mushak_pcb-B_Mask.gbr, mushak_pcb-B_Paste.gbr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]
2022-10-17 Updated PCB with HTSSOP16 package for DRV8833
    [BoM.xlsx, DRV8833.kicad_sch, DRV8833PWPR.step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]
2022-10-17 updated renders
    [mushak_pcb.kicad_pcb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]
2022-10-17 Update schematic
2022-10-17 Update PCB renders
    [mushak_pcb-B_Cu.gbr, mushak_pcb-B_Mask.gbr, mushak_pcb-B_Paste.gbr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]
2022-10-17 Modified Via Placement
    [mushak_pcb-B_Cu.gbr, mushak_pcb-B_Mask.gbr, mushak_pcb-B_Paste.gbr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]
2022-11-02 Add ADC support and example
2023-04-07 Update Mushak PCB design to include new features (#5)
    * Update mushak PCB with new changes
    * Add AMS1117 as 3.3v regulator
    * Add new alternate placement for IR sensors
    * Add new 3.3v compatible ToF sensor
    * Update gerber files
    * Add changes to silkscreen and filter capacitors
    [AMS1117-3.3.step, AS5048_left.kicad_sch, AS5048_right.kicad_sch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]
2023-10-09 Add logging driver library with arm semihosting support
2023-10-14 Add pwm and drv88333 driver
2023-10-14 Add Driver for ADC
    * Add api to access IR sensor
    * Add api for reading battery voltage

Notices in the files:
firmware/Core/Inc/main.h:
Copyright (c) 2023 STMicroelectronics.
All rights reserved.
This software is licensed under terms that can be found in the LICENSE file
